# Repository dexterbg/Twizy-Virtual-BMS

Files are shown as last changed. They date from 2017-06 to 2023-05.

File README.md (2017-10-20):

# Twizy Virtual BMS

This is an Arduino library providing an emulation of the CAN communication protocol of the BMS (battery management system) on a Renault Twizy.

By reproducing the system interface of the original BMS, the Virtual BMS enables replacing the original by a custom battery without changing anything else on the Twizy.

Twizy Virtual BMS

The library provides an API to control power limits and charge current, so a wide range of batteries can be used. Even lead-acid is an option.

In the most simple case this can be used without any customization. The provided "SimpleBMS" example shows how to create a very basic battery monitoring by using the Arduino analog ports to measure the battery pack voltage and temperature.

If you'd like to contribute a specific BMS adaptation, please fork and add your code in the examples folder.

## Installation

To download, click the DOWNLOADS button in the top right corner, download the ZIP file. Start the Arduino IDE, select menu Sketch → Include Library → Add .ZIP library, select the ZIP file and click OK. Try out the examples included.

You will also need these libraries:
  - [MCP_CAN_lib by Cory Fowler](https://github.com/coryjfowler/MCP_CAN_lib)
  - …and one of…
    - [TimerOne by Paul Stoffregen](https://github.com/PaulStoffregen/TimerOne)
    - [FlexiTimer2 by Paul Stoffregen](https://github.com/PaulStoffregen/FlexiTimer2)
    - [TimerThree by Paul Stoffregen](https://github.com/PaulStoffregen/TimerThree)

To get the smallest possible ROM & RAM footprint, set `TWIZY_DEBUG_LEVEL` to 0 and `DEBUG_MODE` of the MCP_CAN library to 0. This reduces the core memory usage of the VirtualBMS library to (currently) 8338 bytes ROM and 403 bytes RAM.

## Documentation

  - [API reference](API.md)
  - [History](HISTORY.md)

  - [Twizy CAN object dictionary](https://docs.google.com/spreadsheets/d/1gOrG9rnGR9YuMGakAbl4s97a6irHF6UNFV1TS5Ll7MY)
  - [Twizy BMS protocol](extras/Protocol.ods)

  - [Battery connection scheme](extras/Twizy-BMS-wiring-scheme.pdf)
  - [List of parts](extras/Twizy-Battery-Part-List.md)

  - [SEVCON configuration](extras/SEVCON-Configuration.md)
  - [Charger configuration](extras/CHARGER-Configuration.md)

  - [Prototype (Lead acid)](extras/Prototype-Blazej.md)
  - [Build #2 (Leaf cells)](extras/Blazej2-Leaf-Cells.md)

## Hardware requirements

  - **Battery**: you will need battery cells capable of producing enough voltage and current for the Twizy. You don't need to exactly match the original voltage and power range. The SEVCON G48 series can operate with input voltages from 19.3 to 69.6 V. The Twizy SEVCON is by default configured for a range of 39 to 65 V, but that can be modified (see [SEVCON configuration](extras/SEVCON-Configuration.md)). In standard configuration, the Twizy will draw up to ~330 A or 16 kW from the battery, and recuperate at up to ~70 A or 3.5 kW. If your battery cannot cope with this, you can either use the Virtual BMS to lower the limits or modify the SEVCON configuration.
  
    Pascal is using Nissan Leaf cells, which offer a very good combination of capacity, availability and price. Błażej is using cheap 120 Ah lead acid batteries (price ~400 Euro for a complete set). Klaus will use chinese prismatic cells adding up to ~12 kWh.
    
    **Note**: Klaus offers to organize a bulk order of high capacity prismatic 3.2V LiFePO4 cells in the range of 330€ down to 260€/kWh. For a high performance large capacity setup with 48V 240 Ah (double of the standard battery capacity) a total price only for the battery pack between 2800 and 3200€ seems possible. Each buyer would have the risk in case of failures and should add some spare cells. For details please contact Klaus at <klauszinser@posteo.eu>.
  
  - **BMS**: using a BMS is optional for lead acid batteries but _strongly recommended_ for lithium based batteries. You may pick any BMS, but you should focus on those that can be connected to the Arduino to query the battery state. Our recommendation is picking a good BMS capable of early balancing, monitoring the coulomb (Ah) consumption and calculating the real SOC.

    **Note**: Pascal is developing a **fully integrated BMS solution** supporting various cell & chemistry configurations and containing the complete Twizy interface. The BMS should be available by the end of 2017. Pricing is expected to be around 350 Euro. Using this BMS will both simplify custom battery integration and reduce points of failure. You won't need an Arduino when using this BMS. For details please contact him at <pascal@ripp.li>.

  - **Arduino**: to run the Twizy Virtual BMS you will need some Arduino and some MCP CAN interface. A wide range of hardware options is available. The code perfectly fits into an Arduino Nano leaving enough memory to implement quite complex custom logics. You should pick an MCP 2515 SPI CAN module with at least 16 MHz clock rate. IRQ connection is optional.

    **Note**: Michael offers to customize the Virtual BMS for individual applications and BMS integration. For details please contact him at <dexter@dexters-web.de>.

  - **Connection**: see the [part list](extras/Twizy-Battery-Part-List.md) for relais and connectors needed.

  - **Battery case**: you can use the original Twizy battery case, available as a replacement part from Renault (see part list).
  
    **Note**: Lutz Schäfer offers to build individual custom battery cases offering more space. For details please contact him at <aquillo@t-online.de>.

## Compliance

As the Virtual BMS (as well as the OVMS and other Twizy tools) is based on re-engineering of the CAN protocol, a 100% compliance cannot be reached. There are still unknown fields and codes, look for question marks in the CAN object dictionary for details. Unknown parts may have an effect under special conditions that could not be produced during analysis.

Having said that, the BMS protocol emulation has successfully been tested and is actually being used in real Twizys, enabling the full standard operation using custom batteries.

If you encounter any kind of issue, please send us all details including a full CAN trace for analysis.

## Projects using this library

  - [KlausBMS Twizy Lithium BMS](https://github.com/dexterbg/KlausBMS)

## Authors

This library has been created and is maintained by Michael Balzer (<dexter@dexters-web.de> / https://dexters-web.de/).

The CAN & hardware protocol decoding and reengineering has been done by a joint effort of (in reverse alphabetical order):

  - Lutz Schäfer <aquillo@t-online.de> -- Hardware development
  - Pascal Ripp <pascal@ripp.li> -- Hardware protocol decoding & implementation
  - Bernd Eickhoff <b.eickhoff@gmx.de> -- CAN logging & testing
  - Michael Balzer <dexter@dexters-web.de> -- CAN protocol decoding & implementation

Special thanks to Klaus Zinser <klauszinser@posteo.eu> for support and to Błażej Błaszczyk <blazej.blaszczyk@pascal-engineering.com> for prototype implementation and testing!

Btw: we're all available for **consulting**, **integration** and **customization** jobs.

## Donations



**Donations** to support our efforts and further development are very welcome.  
Please send donations via **Paypal** to: `virtualbms@dexters-web.de`  
**Thanks! :-)**

Donors will be honored in our [Hall of Eternal Fame](DONORS.md), please add a comment to your donation if you'd rather stay anonymous.

## License

This library is free software; you can redistribute it and/or modify it under the terms of the [GNU Lesser General Public License](https://www.gnu.org/licenses/lgpl.html) as published by the Free Software Foundation; either version 3 of the License, or (at your option) any later version.

This library is distributed in the hope that it will be useful, but WITHOUT ANY WARRANTY; without even the implied warranty of MERCHANTABILITY or FITNESS FOR A PARTICULAR PURPOSE.  See the GNU Lesser General Public License for more details.

You should have received a copy of the GNU Lesser General Public License along with this library; if not, write to the Free Software Foundation, Inc., 51 Franklin St, Fifth Floor, Boston, MA  02110- 1301  USA

**Have fun!**

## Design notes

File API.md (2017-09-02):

# API & Usage

Hint: begin with the "Template" example to get a standard usage template including all callbacks.

## Library inclusion

  1. Create a TwizyVirtualBMS object (`twizy` is a good name for this)
  2. Call `twizy.begin()` in your setup function
  3. Call `twizy.looper()` in your main loop:
        ```c++
        #include "TwizyVirtualBMS_config.h"
        #include "TwizyVirtualBMS.h"
        
        TwizyVirtualBMS twizy;
        
        void setup() {
          Serial.begin(115200);
          twizy.begin();
        }
        
        void loop() {
          twizy.looper();
        }
        ```

## Twizy control functions

Note: all control functions validate their parameters. If you pass any value out of bounds, nothing will be changed, an error message will be generated on the serial port and the function will return `false`.

  - `bool setChargeCurrent(int amps)` -- Set battery charge current level
    - amps: 0 .. 35 A current level at battery
    - will stop charge if set to 0 while charging
    - Note: this has a 5 A resolution rounded downwards
    - Note: 35 A will not be reached with current charger generation (max ~32 A)

      | Current level | Power drawn from socket |
      | ------------- | ----------------------- |
      | 35 A          | ~ 2.2 kW                |
      | 30 A          | ~ 2.1 kW                |
      | 25 A          | ~ 1.7 kW                |
      | 20 A          | ~ 1.4 kW                |
      | 15 A          | ~ 1.0 kW                |
      | 10 A          | ~ 0.7 kW                |
      |  5 A          | ~ 0.4 kW                |

  - `bool setCurrent(float amps)` -- Set momentary battery pack current level
    - amps: -500 .. +500 (A, positive = charge, negative = discharge)
  
  - `bool setCurrentQA(long quarterAmps)` -- Set momentary battery pack current level
    - quarterAmps: -2000 .. +2000 (1/4 A, positive = charge, negative = discharge)
    - This is the native BMS current resolution, so no float/division necessary
  
  - `bool setSOC(float soc)` -- Set state of charge
    - soc: 0.00 .. 100.00 (%)
    - Note: the charger will not start charging at SOC=100%
  
  - `bool setPowerLimits(unsigned int drive, unsigned int recup)` -- Set SEVCON power limits
    - drive: 0 .. 30000 (W)
    - recup: 0 .. 30000 (W)
    - Note: both limits have a resolution of 500 W and will be rounded downwards
    - Note: these limits do not apply if the [SEVCON has been configured](extras/SEVCON-Configuration.md) to ignore them
  
  - `bool setSOH(int soh)` -- Set state of health
    - soh: 0 .. 100 (%)
  
  - `bool setCellVoltage(int cell, float volt)` -- Set battery cell voltage
    - cell: 1 .. 16 (the original Twizy battery has 14 cells)
    - volt: 1.0 .. 5.0
    - Note: this does no implicit update on the overall pack voltage
    - Note: cell voltages #15 & #16 will be stored in frame 0x700 (custom protocol extension)
  
  - `bool setVoltage(float volt, bool deriveCells)` -- Set battery pack voltage
    - volt: 19.3 .. 69.6 (SEVCON G48 series voltage range)
    - deriveCells: true = set cell voltages #1-#14 to volt/14
  
  - `bool setModuleTemperature(int module, int temp)` -- Set battery module temperature
    - module: 1 .. 8 (the original Twizy battery is organized in 7 modules)
    - temp: -40 .. 100 (°C)
    - Note: this does no implicit update on the overall pack temperature
    - Note: module temperature #8 will be stored in frame 0x554 byte 7, which is unused on the original pack layout
  
  - `bool setTemperature(int tempMin, int tempMax, bool deriveModules)` -- Set battery pack temperature
    - tempMin: -40 .. 100 (°C)
    - tempMax: -40 .. 100 (°C)
    - deriveModules: true = set module temperatures #1-#7 to avg(min,max)
  
  - `bool setError(unsigned long error)` -- Set display error/warning indicators
    - error: 0x000000 .. 0xFFFFFF (0 = no error) or use a bitwise ORed combination of…

      | Code              | Description                           |
      | ----------------- | ------------------------------------- |
      | `TWIZY_OK`        | Clear all indicators                  |
      | `TWIZY_SERV`      | Set SERV indicator                    |
      | `TWIZY_SERV_12V`  | Set SERV + 12V battery indicator      |
      | `TWIZY_SERV_BATT` | Set SERV + 12V main battery indicator |
      | `TWIZY_SERV_TEMP` | Set SERV + temperature indicator      |
      | `TWIZY_SERV_STOP` | Set SERV + STOP indicator + beep      |

## Info access

  - `int getChargerTemperature()` -- Get internal charger temperature
    - result: -40 .. 100 (°C, resolution 1 °C)
    - Hint: use this to protect the charger against over temperature by reducing the charge current

  - `float getDCConverterCurrent()` -- Get DC/DC converter current level
    - result: 0 .. 51 (A, resolution 1/5 A)

  - `bool isPluggedIn()` -- Get power grid connection status
    - result: true = 230V detected

  - `bool isSwitchedOn()` -- Get key switch status
    - result: true = key turned

## User callback registration

To hook into the control flow you may register custom functions to be called by the VirtualBMS.

All callbacks are optional. See "Template" example for code templates and example attachment.

  - `void attachEnterState(TwizyEnterStateCallback fn)`
    - fn: `void fn(TwizyState currentState, TwizyState newState)`
    - called on all state transitions after framework handling
    - use this to apply custom settings on state changes

  - `void attachCheckState(TwizyCheckStateCallback fn)`
    - fn: `bool fn(TwizyState currentState, TwizyState newState)`
    - called before transitions from `Init`, `Start…` and `Stop…` into `Ready`, `Driving`, `Charging` and `Trickle`
    - if the callback returns false, the transition will be retried on the next 10 ms ticker run
    - use this to check if the battery/BMS is ready for the state transition

  - `void attachTicker(TwizyTickerCallback fn)`
    - fn: `void fn(unsigned int clockCnt)`
    - called by the 10 ms ticker *after* framework handling, i.e. after sending the Twizy CAN frames
    - clockCnt: cyclic 10 ms interval counter range 0 … 2999 (reset to 0 on `Off`/`Init`)
    - use this to add custom CAN sends or do periodic checks

  - `void attachProcessCanMsg(TwizyProcessCanMsgCallback fn)`
    - fn: `void fn(unsigned long rxId, byte rxLen, byte *rxBuf)`
    - called on all received (filtered) CAN messages
    - see `setCanFilter()` for setup of additional custom CAN ID filters

## State machine

The VirtualBMS will do state transitions automatically based on CAN input received from the Twizy.

__TwizyStates:__
  - `Off`
  - `Init`
  - `Error`
  - `Ready`
  - `StartDrive`
  - `Driving`
  - `StopDrive`
  - `StartCharge`
  - `Charging`
  - `StopCharge`
  - `StartTrickle`
  - `Trickle`
  - `StopTrickle`

Normal startup procedure involves the wakeup phase `Init` followed by `Ready`. Depending on the mode of operation requested, this will be followed by one of the `Start…` states with operation mode established resulting in the according `…ing` state.

The shutdown procedure begins with a transition from the `…ing` state to the according `Stop…` state, followed by `Ready` and finally `Off`.

Use the `Error` state to signal **severe problems** to the Twizy and cause an emergency shutdown. `Error` turns off CAN sends and drops the 3MW (ECU_OK) signal. SEVCON and charger will switch off all battery power immediately. To resolve the `Error` state from driving, the user needs to do a power cycle. When used during a charge, the charger will send the BMS into `Off` state, so the charge can simply be restarted by replugging the charger.

**Note**: to indicate **non-critical** problems, do not enter the `Error` state but instead only use `setError()`.

See [protocol documentation](extras/Protocol.ods) for details.

__API:__
  - `TwizyState state()` -- Query current state
  - `FLASHSTRING *stateName([state])` -- Query name of current state / specific state
  - `bool inState(TwizyState state1 [, … state5])` -- Test for 1-5 states
  - `void enterState(TwizyState newState)` -- Force a state change
    - Call `enterState(StopCharge)` to stop a running charge process. Note that `setChargeCurrent(0)` will do so as well.
    - Call `enterState(Error)` to cause an emergency shutdown. Before doing this you should use `setError()` and (if possible) give the user some time to react when in state `Driving`.

__Callbacks:__
  - Before entering states `Ready`, `Driving`, `Charging` and `Trickle` from any other state, the user callback `CheckState()` will be called.
    Exception is entering `Ready` from `Error`, this needs to be done manually anyway (don't expect SEVCON or charger to follow though).
  - After any state transition, the user callback `EnterState` will be called.

## CAN interface access

To hook into the CAN receiver, use `attachProcessCanMsg()` (see above).

Standard filters will pass IDs `0x423`, `0x597` and `0x599`. Three free CAN filters can be used. The mask is fixed to match the whole ID, so you can filter at most three additional IDs at a time.

  - `void setCanFilter(byte filterNum, unsigned int canId)` -- Set a free ID filter
    - filterNum: 1 … 3
    - canId: 11 bit CAN ID i.e. `0x196`

  - `bool sendMsg(INT32U id, INT8U len, INT8U *buf)` -- Send a CAN message
    - Note: will do three retries if TX buffers are full.
    - Returns true if message has been sent, false on error.
    - Retry and error counts are logged every 10 seconds if debug logging is enabled.

## Debug utils

  - `void dumpId(FLASHSTRING *name, int len, byte *buf)` -- Dump a byte buffer in hex numbers
    - name: must be a PROGMEM string, i.e. `dumpId(F("id123"), ...)`
  
  - `void debugInfo()` -- Dump VirtualBMS status, include frame buffers if debug level >= 2
    - this is automatically called every 10 seconds if debug level >= 1

## Extended info frame

Beginning with version 1.3.0, the VirtualBMS supports sending an extended BMS status information on the CAN bus. The frame layout has been designed by Pascal Ripp and Michael Balzer to create a standard base for CAN bus tools like the Twizplay and the OVMS.

The extended info frame is sent at CAN ID 0x700 once per second in all states except `Off`. The frame transports these fields:

  - Byte 0: BMS specific state #1 (main state, i.e. twizy.state())
  - Byte 1: highest 3 bits = BMS type ID (see below), remaining 5 bits = BMS specific error code (see below)
  - Bytes 2-4: cell voltages #15 & #16 (encoded in 12 bits like #1-#14)
  - Bytes 5-6: balancing status (bits 15…0 = cells 16…1, 1 = balancing active)
  - Byte 7: BMS specific state #2 (auxiliary state or data)

The VirtualBMS will not send frame 0x700 unless you set the BMS type. It will also not insert any data into the fields by itself, to fill in data you need to use the API calls as shown below. This way you can use the VirtualBMS library to implement other BMS types as well.

### BMS types

The BMS type is meant for CAN tools to be able to identify the BMS and decode the BMS specific states and error info.

There are currently 7 possible BMS types, defined in `enum TwizyBmsType`:

  - 0 = `bmsType_VirtualBMS` (states and error codes as documented here)
  - 1 = `bmsType_EdriverBMS` (see Pascal's documentation for details)
  - 2…6 = reserved
  - 7 = `bmsType_undefined` (disables frame 0x700)

Types #2…#6 can be assigned to future BMS types.

Please contact us if you want to allocate an ID. Keep in mind: any new BMS type needs support in all CAN tools, so try to reuse one of the already defined BMS types as long as possible.

### BMS error codes (for `bmsType_VirtualBMS`)

Our basic standard proposition covers these error codes (defined in `enum TwizyBmsError`):

  - 0 = `bmsError_None`
  - 1 = `bmsError_EEPROM`
  - 2 = `bmsError_SensorFailure`
  - 3 = `bmsError_VoltageHigh`
  - 4 = `bmsError_VoltageLow`
  - 5 = `bmsError_VoltageDiff`
  - 6 = `bmsError_TemperatureHigh`
  - 7 = `bmsError_TemperatureLow`
  - 8 = `bmsError_TemperatureDiff`
  - 9 = `bmsError_ChargerTemperatureHigh`

Custom error codes can be added beginning at 128. Please contact us if you'd like to add standard error codes.

### API calls

  - `bool setInfoBmsType(byte bmsType)` -- Set informational BMS type
    - bmsType: 0 .. 7 (see above / enum TwizyBmsType)
    - Note: type 7 (bmsType_undefined = default value) deactivates frame 0x700

  - `bool setInfoState1(byte state)` -- Set informational state 1 (main state)
    - state: 0x00 .. 0xFF (specific by BMS type)

  - `bool setInfoState2(byte state)` -- Set informational state 2 (aux state)
    - state: 0x00 .. 0xFF (specific by BMS type)

  - `bool setInfoError(byte errorCode)` -- Set informational error code
    - errorCode: 0x00 .. 0x1F (specific by BMS type)

  - `bool setInfoBalancing(unsigned int flags)` -- Set informational balancing status
    - flags: 16 bits = 16 cells (#16 = MSB, #1 = LSB), 1 = balancing

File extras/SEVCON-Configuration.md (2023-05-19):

# SEVCON Configuration

You do not need to change the SEVCON configuration to use a custom battery if the custom battery delivers voltage and power matching the standard operating range and your SEVCON battery protection has not been disabled.

- The SEVCON G48 series can operate with input voltages from 19.3 to 69.6 V. The Twizy SEVCON is by default configured for a range of 39 to 65 V.
- In standard configuration, the Twizy will draw up to ~330 A or 16 kW from the battery, and recuperate at up to ~70 A or 3.5 kW.

If your battery cannot cope with these limits, you can either use the Virtual BMS to lower the limits or modify the SEVCON configuration.

If you need to set the limits regularly below the standards, consider tuning the Twizy down. Triggering the power limiter will result in a sudden power cutback followed by slowly raising power levels until the limit is reached again. This continues over and over leading to an inconvenient pumping effect.

**Note**: SEVCON write access has been limited by Renault on Twizys (SEVCONs) delivered after June 2016. The write protection applies to all power and driving profile tuning registers, and also to the voltage limits. **If you've got a locked Twizy, your battery should match the standard battery parameters.**

A locked SEVCON will respond to register writes with an error. You can also check the software version (`rs 100a 00`): if it's `0712.0003` or higher, the Twizy is locked.

## Tools

You can configure the SEVCON using…

1. [Official SEVCON tools](http://www.sevcon.com/products/low-voltage-controllers/gen4/)
2. [OVMS](https://github.com/openvehicles/Open-Vehicle-Monitoring-System)
3. [Twizy-Cfg for Arduino](https://github.com/dexterbg/Twizy-Cfg)
4. Generic CANopen editor

The syntax for reading/writing the SEVCON registers slightly varies depending on the software used, but the registers and values are the same.

| Function | Twizy-Cfg | OVMS |
| --- | --- | --- |
| Enter pre-op mode | `p` | `cfg pre` |
| Enter op mode | `o` | `cfg op` |
| Read register | `r <id> <sub>` | `cfg read <id> <sub>` |
| Write register | `w <id> <sub> <val>` | `cfg write <id> <sub> <value>` |

The following command examples use the Twizy-Cfg syntax.

**Note**: negative values currently need to be read and written with value offset 65536 ("complementary"), i.e. -1 = 65535.

## Battery voltage limits

| Register | Description | Default | Scaling | …= |
| --- | --- | --- | --- | --- |
| `2c01 01` | Over voltage start cutback | 992 | 1/16 | 62 V |
| `2c01 02` | Over voltage limit | 1040 | 1/16 | 65 V |
| `2c02 01` | Under voltage start cutback | 656 | 1/16 | 41 V |
| `2c02 02` | Under voltage limit | 624 | 1/16 | 39 V |
| `2c03 00` | Protection delay | 80 | 1/10 | 8 s |

**Example**: to allow voltages down to 35 V, issue…

1. `w 2c02 01 592`
2. `w 2c02 02 560`

**Keep in mind** that the SEVCON derives current levels from allowed power levels (unless configured otherwise, see below). A lower voltage will result in higher currents, take care to lower the power limits as necessary using the `setPowerLimits()` API call when your voltage drops.

## Battery current & power limits

**Note**: these only apply to the driving state, the charger current can be controlled by `setChargeCurrent()` regardless of the SEVCON configuration.

| Register | Description | Default | Scaling | …= |
| --- | --- | --- | --- | --- |
| `2870 01` | Battery current limit source | 4 | see below | BMS |
| `2870 02` | Max discharge current | 500 | 1 | 500 A |
| `2870 03` | Max recharge current | 65336 | -1 | 200 A |
| `2870 04` | Profile 1 level | 0 | 1 | 0% |
| `2870 05` | Profile 2 level | 0 | 1 | 0% |
| `2870 06` | _Max discharge power (derived)_ | i.e. 4608 | 1/256 | 18 kW |
| `2870 06` | _Max recharge power (derived)_ | i.e. 64896 | -1/256 | 2.5 kW |
| `4623 01` | _Calculated recharge current limit (power/voltage)_ | 65493 | -1 | 43 A |
| `4623 02` | _Calculated discharge current limit (power/voltage)_ | 314 | 1 | 314 A |
| `4623 03` | Battery current cutback range | 15 | 1 | 15 A |
| `3813 30` | Battery current recovery speed | 100 | 100/256 | 39.0625 %/s |
| `3813 30` | Battery current cutback speed | 800 | 1 | 312.5 %/s |

**Battery current limit source**:
  - `4`: BMS controls power limits through `setPowerLimits()`, current levels calculated from power levels
  - `3`: Use max currents scaled down by profile level (`setPowerLimits()` disabled)
  - `1`: Use max currents (`setPowerLimits()` disabled)
  - `0`: Limiter off (`setPowerLimits()` disabled)

These registers need pre-operational mode to allow writes.

**Example**: to disable `setPowerLimits()` and set a fixed maximum of 250 A for discharge (driving) and 50 A for recharging (recuperation), issue…

1. `p`
2. `w 2870 01 1`
3. `w 2870 02 250`
4. `w 2870 03 65486`
5. `o`

## SOC based power cutbacks

| Register | Description | Default | Scaling | …= |
| --- | --- | --- | --- | --- |
| `3813 11` | Drive cutback map: SOC 1 | 0 | 1/50 | 0 % SOC |
| `3813 12` | … cutback 1 | 750 | 1/50 | 15 % power |
| `3813 13` | … SOC 2 | 750 | 1/50 | 15 % SOC |
| `3813 14` | … cutback 2 | 5000 | 1/50 | 100 % power |
| `3813 15` | Brake cutback map: SOC 1 | 0 | 1/50 | 0 % SOC |
| `3813 16` | … cutback 1 | 5000 | 1/50 | 100 % power |
| `3813 17` | … SOC 2 | 500 | 1/50 | 10 % SOC |
| `3813 18` | … cutback 2 | 5000 | 1/50 | 100 % power |

The SEVCON applies these linear cutbacks based on SOC additionally to the BMS power limits allowing for a smooth cutback slope. Default is to cutback drive power below 15% SOC, and leave brake power at BMS control.

These registers need pre-operational mode to allow writes.

**Example**: configure full brake power cutback from 90% to 100% SOC:

1. `p`
2. `w 3813 15 4500`
3. `w 3813 17 5000`
4. `w 3813 18 0`
5. `o`

## Other configuration options

Read the SEVCON Gen4 manual for some basic description. The full register set is documented in the SEVCON master dictionary, which is ©SEVCON. It's contained in the SEVCON DVT package.

Most registers of interest for normal tuning have been documented in the [OVMS Twizy SDO list](https://github.com/openvehicles/Open-Vehicle-Monitoring-System/raw/master/docs/Renault-Twizy/Twizy-SDO-List.ods).

**Have fun!**

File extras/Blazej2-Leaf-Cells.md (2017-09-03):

# Build #2 by Błażej Błaszczyk using Nissan Leaf cells

Błażejs second battery is based on used Nissan Leaf cells. Błażej bought a used 2015 Nissan 24 kWh pack for 14000 PLN (~3300 EUR).

The 24 kWh pack consists of 48 modules with ~500 Wh each. He disassembled the pack and managed to put 21 modules into the Twizy (tight fit, original case won't fit around these).

This pack uses a simple standard 14 cell hardware BMS for the cell protection and balancing (hosted on the lower PCB). The upper PCB hosts the VirtualBMS Arduino components, basically following the [example scheme](https://github.com/dexterbg/Twizy-Virtual-BMS/blob/master/extras/Twizy-Battery-Part-List.md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). Cell voltages are measured using voltage dividers over a multiplexer, pack current is measured using a LEM hall sensor and temperatures using LM35. An HC-06 module is included for Bluetooth connectivity.

Real world driving range with this 10.5 kWh pack is around 130-140 km. Due to the higher capacity, the battery voltage is more stable than the original battery, even under high load.

If you'd like to know more, contact Błażej Błaszczyk <blazej.blaszczyk@pascal-engineering.com>.

## Images

(click to zoom)

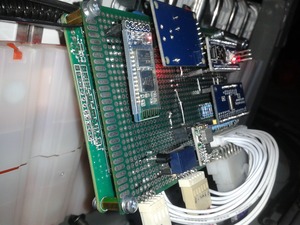
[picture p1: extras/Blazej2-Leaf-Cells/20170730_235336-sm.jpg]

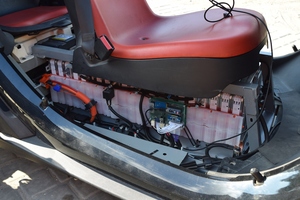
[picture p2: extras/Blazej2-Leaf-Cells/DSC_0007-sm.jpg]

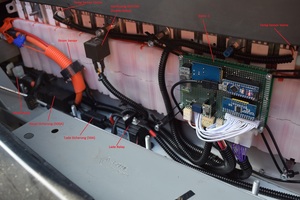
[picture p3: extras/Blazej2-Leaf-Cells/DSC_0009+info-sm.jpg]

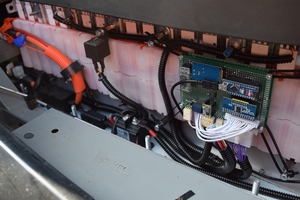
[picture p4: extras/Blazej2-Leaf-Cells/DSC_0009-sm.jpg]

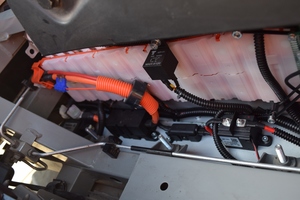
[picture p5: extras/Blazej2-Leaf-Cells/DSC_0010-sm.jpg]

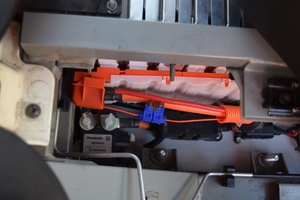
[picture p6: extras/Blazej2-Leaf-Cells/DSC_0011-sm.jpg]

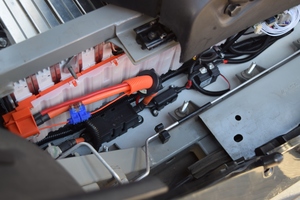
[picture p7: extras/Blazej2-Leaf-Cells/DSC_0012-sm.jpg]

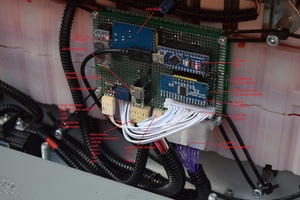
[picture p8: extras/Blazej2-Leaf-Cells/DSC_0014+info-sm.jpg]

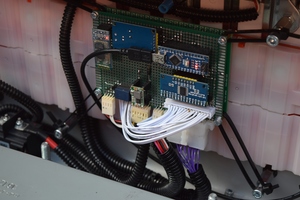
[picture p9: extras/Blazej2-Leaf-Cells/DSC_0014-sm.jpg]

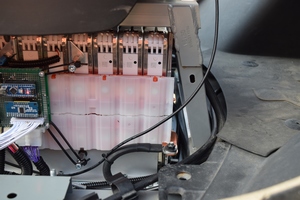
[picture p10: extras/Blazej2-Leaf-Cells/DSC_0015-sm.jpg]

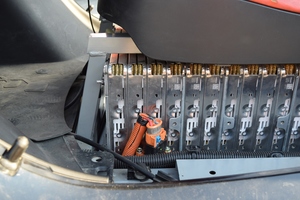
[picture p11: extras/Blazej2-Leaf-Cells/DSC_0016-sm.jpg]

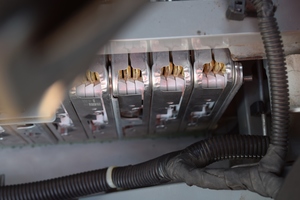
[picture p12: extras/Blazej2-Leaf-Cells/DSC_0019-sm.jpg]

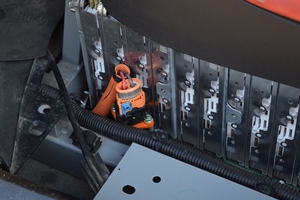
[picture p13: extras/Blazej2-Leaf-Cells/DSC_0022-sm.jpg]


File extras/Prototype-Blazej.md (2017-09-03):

# Prototype build by Błażej Błaszczyk

This is a prototype actually powering Błażejs own Twizy.

It uses four standard 120 Ah lead acid batteries. Range with new batteries is ~ 50-60 km on flat terrain.

No Renault parts have been used. The main power relais is from a fork lift.

There is no BMS other than the Arduino (Nano) itself. The pack voltage is measured using a voltage divider, the pack temperature is measured using an LM35D sensor. SOC is derived from the (smoothed) pack voltage. The software is basically the "SimpleBMS" example from the library with calibration for Błażejs components.

If you'd like to know more, contact Błażej Błaszczyk <blazej.blaszczyk@pascal-engineering.com>.

Please also take a look at [Błażejs build #2](Blazej2-Leaf-Cells.md).

## Videos

(click to watch on Youtube)

Start and GO (https://youtu.be/PRJoss-2DbI "Start and GO")
Drive (https://youtu.be/OG0C9ohnqXw "Drive")

## Images

(click to zoom)

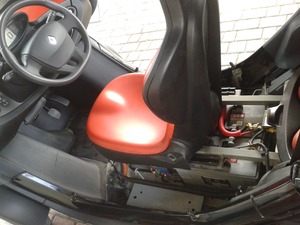
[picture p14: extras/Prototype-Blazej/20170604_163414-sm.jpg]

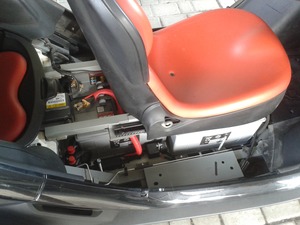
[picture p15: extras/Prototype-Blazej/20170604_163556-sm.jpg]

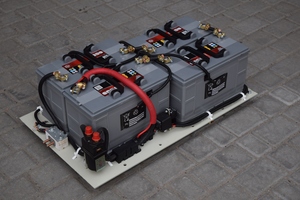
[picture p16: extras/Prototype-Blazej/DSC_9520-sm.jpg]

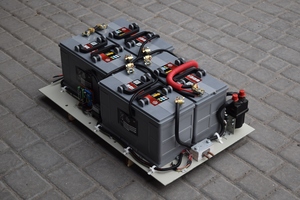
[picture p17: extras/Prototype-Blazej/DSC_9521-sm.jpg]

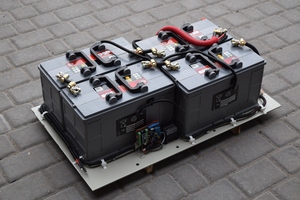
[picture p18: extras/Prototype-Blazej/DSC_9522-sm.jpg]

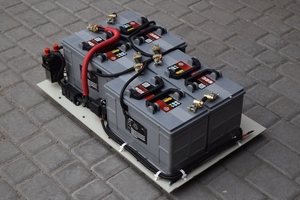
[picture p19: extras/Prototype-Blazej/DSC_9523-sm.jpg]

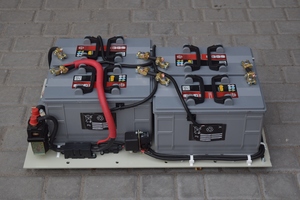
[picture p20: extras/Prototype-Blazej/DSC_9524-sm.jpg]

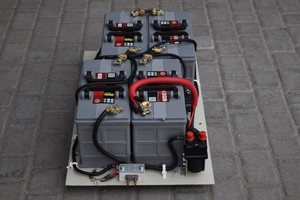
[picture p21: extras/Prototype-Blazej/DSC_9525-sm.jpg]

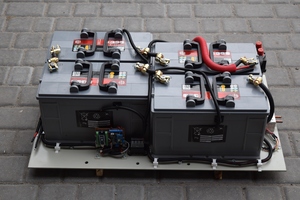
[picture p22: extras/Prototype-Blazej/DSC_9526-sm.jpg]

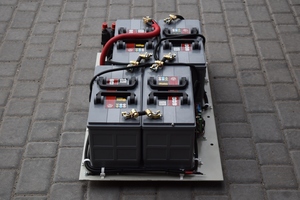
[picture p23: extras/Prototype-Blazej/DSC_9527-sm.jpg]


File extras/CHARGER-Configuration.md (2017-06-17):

# Charger Configuration

You do not need to change the charger if your battery can be charged at the standard voltage and current levels provided by the builtin [IES-Synergy Elips 2000W](http://www.ies-synergy.com/en/chargers/onboard-sealed-chargers/elips-2000w) charger.

- The Elips 2000W can charge with a final voltage of up to 60 V.
- Charge current can be set from 0 - 35 A in 5 A steps.

It may be possible to configure the Elips in the future, at the moment you need to control the charge current and stop the charge process using the `setChargeCurrent()` [API call](../API.md), if your battery cannot cope with the Elips standard charge process.

## Using a custom charger

If you need or want to use a custom charger, take care not to remove the Elips 2000W from the Twizy without further consideration.

The Elips is operating with a specialized firmware and has a crucial role in the Twizy's control protocol.

You can charge a custom battery directly without using the Elips, but for driving and 12V trickle charging the Elips needs to be connected to the battery and CAN bus.

If you're interested in replacing the Elips: creating a "Twizy Virtual Charger" should be possible as well, but has to be done yet.

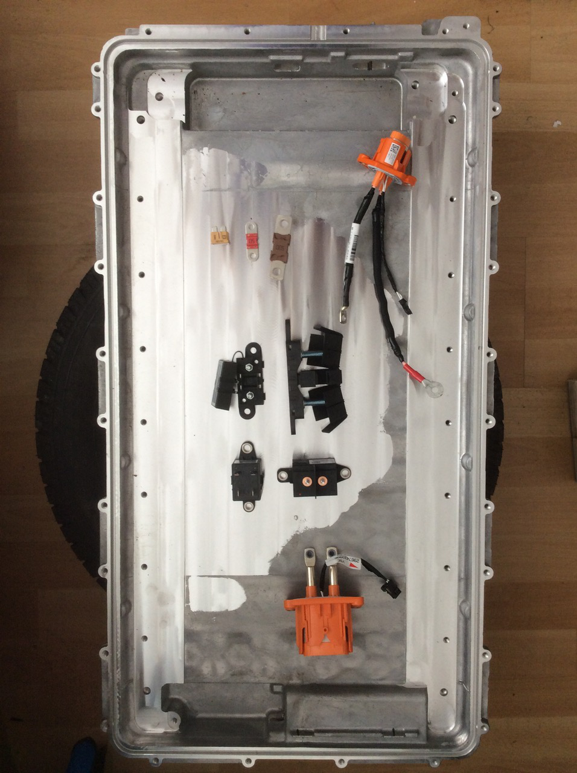
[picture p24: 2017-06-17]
extras/parts/Overview-nm.jpg

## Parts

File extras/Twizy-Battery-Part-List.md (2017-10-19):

# Twizy Battery Part List

For explosion drawings and OE part numbers, see…

1. [partsouq.com](https://partsouq.com/en/catalog/genuine/vehicle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)
2. [catcar.info](https://www.catcar.info/renault/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)

A good source for all parts is [JC Parts](https://www.jcparts.eu/).

## Fuses, connectors and relais

| # | Image | Part | OE number | ~Price |
| --- | --- | --- | --- | --- |
| 1x | 296539341R | Fusible Principal Fltg Ent Chr <br/> *Main fuse 500A* | 296539341R | 4.41 € |
| 1x | 296539051R | Fusible Chargeur Fltg Ent Chrj <br/> *Charge fuse 50A* | 296539051R | 1.67 € |
| 1x | 296535672R | Fusible Apres Contact Fltg Ent <br/> *Precharge fuse 5A* | 296535672R | 1.30 € |
| 1x | 296713282R | Platine Fusible <br/> *Main fuse holder* | 296713282R | 10.48 € |
| 1x | 296712452R | Platine Fusible <br/> *Charge fuse holder* | 296712452R | 7.96 € |
| 1x | 296743399R | Embase Connecteur Batterie Tra <br/> *Main connector (DELPHI)* | 296743399R | 52.22 € |
| 1x | 296746418R | Embase Connecteur Ba <br/> *Charge connector (DELPHI)* | 296746418R | 30.67 € |
| 1x | 296740718R | Embase Connecteur <br/> *Signal connector (Yazaki)* | 296740718R | 86.30 € |
| 1x | 294B16331R | Relais Principal Boitier Cnx P <br/> *Main relais 150A* | 294B16331R | 56.63 € |
| 1x | 294B20431R | Relais Precharge Boitier Cnx P <br/> *Precharge relais 10A* | 294B20431R | 21.19 € |
| 1x | 296156226R | Relais Chargeur Fltg Ent Chrjr <br/> *Charge relais 40A* | 296156226R | 39.96 € |
| | | **Total**  *(prices may change)* | | **~ 310 €** |

Parts may of course be replaced by functionally compatible ones, for example use a fork lift relais for the main power relais (relais & fuses are no special parts). Błażej Błaszczyk has built his [prototype](Prototype-Blazej.md) without using Renault parts. For details please contact him at <blazej.blaszczyk@pascal-engineering.com>.

  - The `296740718R` signal connector is Yazaki part no. [7282-8854-30](http://connectors-catalog.sys.yzk.co.jp/yazaki-web/servlet/SubServlet_e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) (contact terminals sold separate).
  - The `296743399R` main power connector is DELPHI part no. [F473110](http://ecat.delphi.com/feature?search=F473110), with contact terminals [F176600](http://ecat.delphi.com/feature?search=F176600).
  - The `296746418R` charger power connector is DELPHI part no. [F873110](ecat.delphi.com/feature?search=F873110), with contact terminals [15516298](http://ecat.delphi.com/feature?search=15516298).

## Casing

| # | Image | Part | OE number | ~Price |
| --- | --- | --- | --- | --- |
| 1x | 295F00162R | CARTER SUP BATTERI	<br/> *Casing cover* | 295F00162R | 129 € |
| 1x | 295F19016R | CARTER INF BATTERI <br/> *Casing base* | 295F19016R | 216 € |
| 1x |  | JOINT ETC CARTER B <br/> *Casing seal* | 295G32560R | 46 € |
| | | **Total**  *(prices may change)* | | **~ 390 €** |

**Note**: Lutz Schäfer offers to build individual custom battery cases offering more space. For details please contact him at <aquillo@t-online.de>.

__Sizes__:
  - Standard Renault Box: 724 x 368 x 208 mm
  - Lutz-Box V1 (without car modification): 745 x 400 x 245 mm
  - Lutz-Box V2 (car modification necessary): 745 x 480 x 245 mm

## Arduino

**Note**: if you plan to use **Pascals integrated Twizy BMS**, you won't need an Arduino. The integrated BMS also implements the Twizy protocol.

For a basic setup you'll need an Arduino, a CAN interface and a relais to switch the 3MW signal.

If you want/need to measure cell voltages and temperatures with the Arduino, you will most probably need some analog input extension. A very simple and cheap setup for up to 16 cells is to use an analog multiplexer based on the CD74HC4067 chip.

Standard Arduinos can be powered from 12V, but will burn the voltage difference (convert to heat), so a step-down voltage regulator is highly recommended. The [Pololu A-Star SV series](https://www.pololu.com/category/149/a-star-programmable-controllers) has on-board step-down regulators suitable for a 12V supply.

Using an Arduino Uno style main board with shields reduces soldering requirements but needs more money and space than for example a Nano based board with break out components.

Keep in mind for all setups, this is an automotive application: expect high levels of mechanical stress due to road shocks and temperature expansion/contraction. Protect your electronics against humidity.

**Price note**: there are lots of cheap Arduino clones available. These can of course be used as well. Expect a lower build quality, so better order some spares (always a good idea).

### Example basic Uno/Shield setup

| Category | Component | ~Price |
| --- | --- | --- |
| Main+Power | Pololu A-Star 32U4 Prime SV | 24.95 € |
| CAN | Seeed Studio CAN-BUS Shield v1.2 | 24.95 € |
| Relais | Seeed Studio Relais Shield V3.0 | 21.95 € |
| **Total** | | **~ 72 €** |

### Example basic Nano setup

| Category | Component | ~Price |
| --- | --- | --- |
| Main | Arduino Nano V3 clone | 4.95 € |
| I/O | Arduino NANO Screw Terminal Expansion Board | 4.95 € |
| CAN | NiRen MCP2515_CAN (TJA1050) | 4.50 € |
| CAN | … 16 MHz quartz | 0.23 € |
| Relais | 5V 2 Channel Relay Shield | 2.95 € |
| **Total** | | **~ 18 €** |

### Example components

| Category | Component | ~Price |
| --- | --- | --- |
| Main | Arduino Uno R3 | 20.80 € |
| Main | Arduino Nano V3 | 23.80 € |
| Main+Power | Pololu A-Star 32U4 Prime SV | 24.95 € |
| Power | Pololu 5V, 2.5A Step-Down Voltage Regulator D24V22F5 | 8.95 € |
| CAN | Seeed Studio CAN-BUS Shield v1.2 | 24.95 € |
| CAN | NiRen MCP2515_CAN (TJA1050) <br/> *Note: these come with 8 MHz quartz, you should replace this with a 16 MHz type* | 4.50 € |
| Relais | Seeed Studio Relais Shield V3.0 | 21.95 € |
| Relais | 5V 2 Channel Relay Shield | 2.95 € |
| I/O | Adafruit Proto-Screwshield | 15.50 € |
| I/O | Arduino NANO Screw Terminal Expansion Board | 4.95 € |
| I/O | SparkFun Analog/Digital MUX Breakout - CD74HC4067 (16 Channel) | 4.95 € |
| I/O | Adafruit ADS1015 12-Bit ADC - 4 Channel | 10.95 € |
| I/O | Mayhew Labs Extended ADC Shield | 30 € |
| I/O | Seeed Studio RS232 Shield | 12.50 € |
| I/O | HC-05 Bluetooth module | 6.00 € |

### Example Arduino wiring scheme

This example setup could be used for a battery pack with a very basic BMS that does only cell protection and has no communication interface. So the Arduino is used to monitor cell voltages, pack current and temperature. This is all optional -- basically you could derive the SOC estimation from just the overall pack voltage as well.

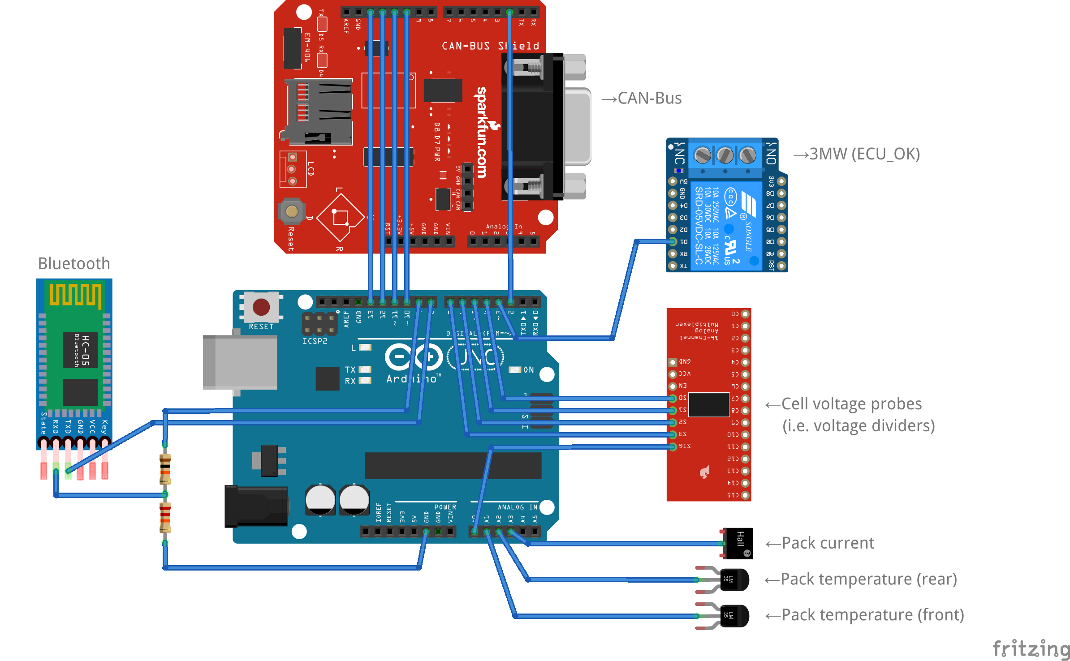
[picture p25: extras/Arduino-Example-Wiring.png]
Arduino Example Wiring


  - [PDF](Arduino-Example-Wiring.pdf)
  - [Fritzing file](Arduino-Example-Wiring.fzz)

The Fritzing diagram only shows the I/O connections, but there's little more: add power supply and enable the multiplexer permanently (connect pin EN to VCC). Obviously, when using a CAN shield like shown in the diagram, it's wiring is done by mounting the shield.

The bluetooth module is optional but neat, it enables to check your VirtualBMS output with a smartphone.

Cell voltages can be measured using the multiplexer shown and simple voltage dividers measuring the stacked voltages, but keep in mind you lose precision by the scaling. The Arduino analog ports provide 10 bit resolution on the voltage range of 0-5 V = ~5 mV. So when scaling to 60 V, resolution drops to ~60 mV. This is good enough to detect a bad cell, but not for precise health monitoring. You may use ADC shields with higher resolution and/or differential voltage probes to get the single cell voltages, but when thinking about this, take a look at specialized battery monitoring chips like the MAX11080 or LTC6811 first.

The pack current can be measured using either a shunt (with an [instrumentation amplifier](http://www.vwlowen.co.uk/arduino/current/current.htm) or an [ADC with preamp](http://arduinotronics.blogspot.de/2015/05/reading-current-shunt-with-arduino.html)) or a hall sensor module like the [LEM HAC 600-S](http://www.lem.com/hq/de/component/option,com_catalog/task,displaymodel/id,64.05.52.000.0/) or the [Tamura L06P400S05](http://www.tamuracorp.com/clientuploads/pdfs/engineeringdocs/L06PXXXS05.pdf). The LEM outputs -4…+4 V so needs to be mapped to the Arduino's 0…5 V (i.e. using an offset voltage divider), the Tamura outputs 0…5 V (2.5 V = 0 A) so can be used directly.

The temperatures can be measured using LM35 sensors. Depending on the variant used, voltage may need to be mapped to the Arduino input. If you want to measure every single cell temperature, you can also extend the setup by another MUX for the temperature sensors -- just use the same address pins as for the voltage MUX.

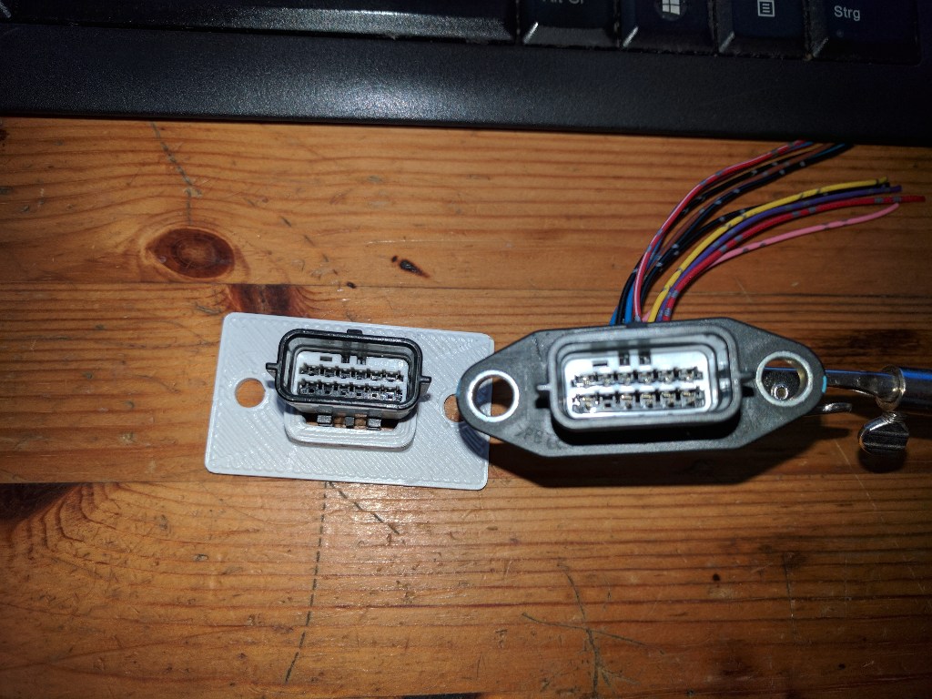
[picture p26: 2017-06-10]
extras/parts/296740718R-tapping.jpg

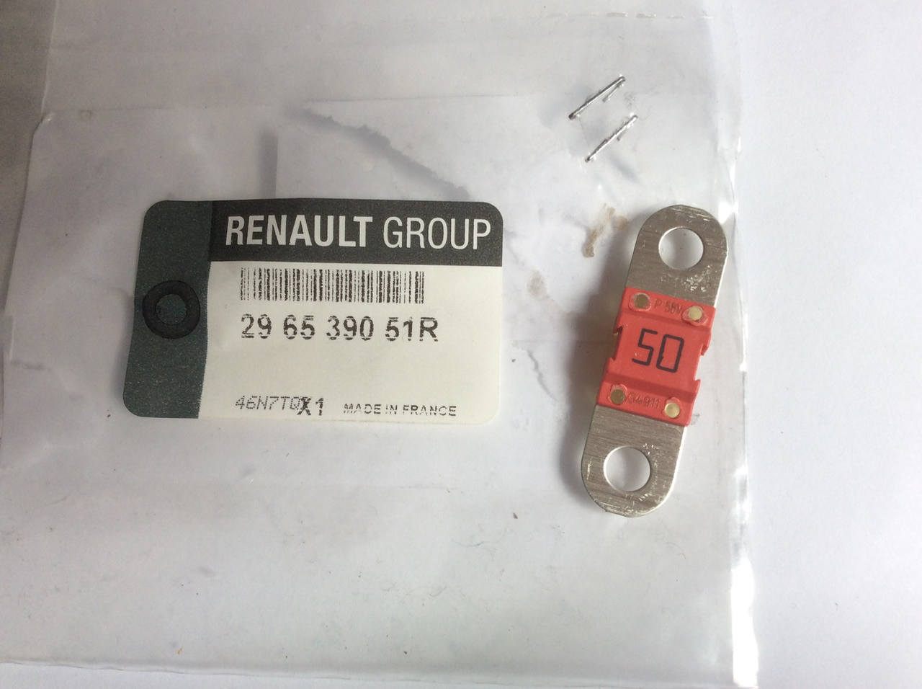
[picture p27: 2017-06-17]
extras/parts/296539051R-nm.jpg

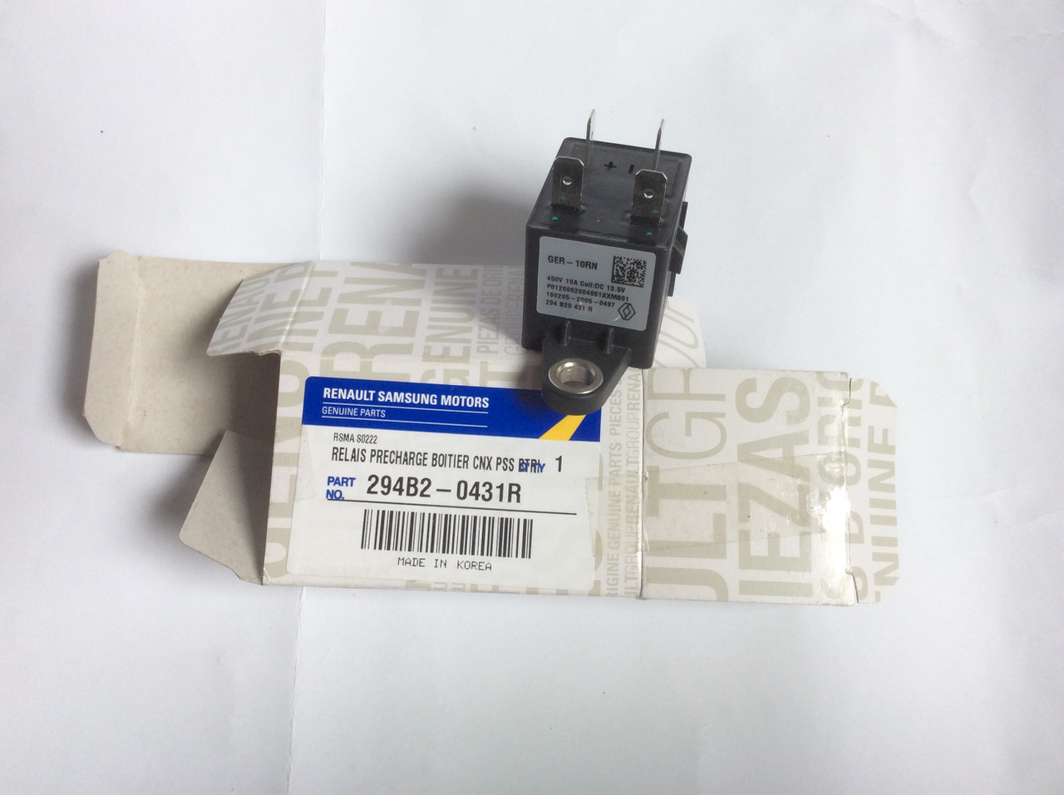
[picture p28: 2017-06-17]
extras/parts/294B20431R-nm.jpg

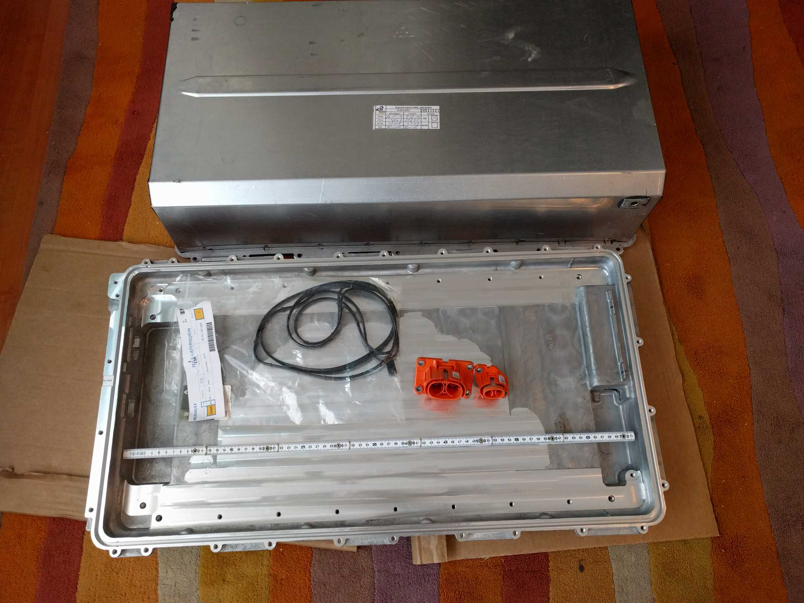
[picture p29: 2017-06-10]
extras/parts/295F00162R-nm.jpg

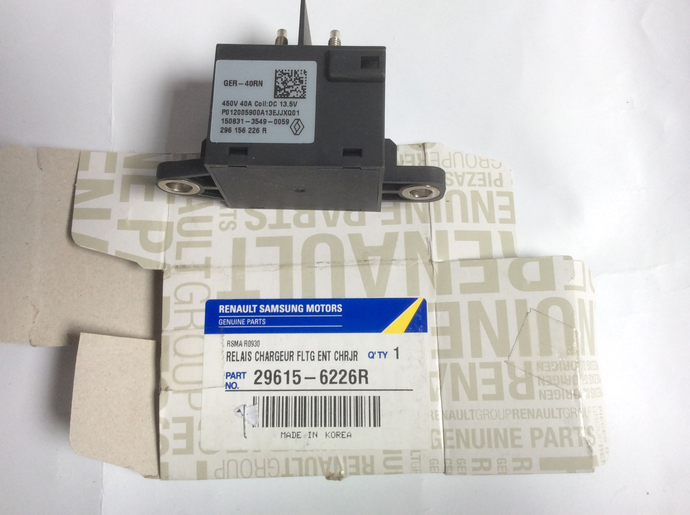
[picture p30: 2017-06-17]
extras/parts/296156226R-nm.jpg

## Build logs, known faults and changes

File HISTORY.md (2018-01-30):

# History

## Version 1.4.4 (2018-01-21)

- Solved issue #1 (charger compatibility)
- Closer reproduction of init phase frames
- Detection of wakeup & shutdown by CAN activity

## Version 1.3.0 (2017-08-30)

- Added support to generate extended info frame 0x700
- New API calls: setInfoBmsType(), setInfoState1(), setInfoState2(), setInfoError(), setInfoBalancing()
- Added support for module temperature #8 and cell voltages #15/#16

## Version 1.2.1 (2017-08-17)

- New API calls stateName(), stateName(state)
- No out of bounds error messages in TWIZY_DEBUG_LEVEL 0

## Version 1.2.0 (2017-07-29)

- Ticker increments clockCnt on exit (first hook call with clockCnt=0)
- Protocol startup phase closer to original:
  - id155[0] set to 0xFF on Init
  - Transition from Init to Ready after 100 ms
  - 3MW timing changed to 200 ms
  - id155[3] update coupled to 3MW switch
- Added API functions to query charger infos:
  - int getChargerTemperature();
  - float getDCConverterCurrent();
  - bool isPluggedIn();
  - bool isSwitchedOn();

## Version: 1.1.0 (2017-06-20)

- Added support for Timer2 & Timer3 (see config header)
- Added `setCurrentQA()` API call (native=fast 1/4 A resolution)

## Version: 1.0.0 (2017-06-17)

- Conversion to Arduino library
- Added CAN RX callback `ProcessCanMsg`
- Added `setError()` and error codes
- Using ROM strings to save RAM
- Configurable debug output level
- Added example Template
- Added example SimpleBMS
- Added `setCanFilter()`
- Added API documentation
- Added hardware documentation
- Added SEVCON configuration info
- Added charger configuration info
- Protocol documentation update on error codes
- Added `Error` state for emergency shutdowns
- Ticker callback also called in state `Off`
- Added donation info & donors file
- Added parts images
- Added inState() test functions
- Added Arduino components to parts list
- Added overview text for Blazejs prototype

## Version: 0.2 (2017-06-06)

- 3MW pulse cycle
- Separate states for trickle charging
- CAN TX retries
- Added bmsTicker() callback

## Version: 0.1 (2017-06-04)

- Initial release

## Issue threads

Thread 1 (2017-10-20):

Charger compatibility

dexterbg, 2017-10-20:
Blazej has reworked a handfull Twizys using the VirtualBMS and has found an issue: the current VirtualBMS implementation does only work with chargers up to generation 5 (charger label: "Ind …"). Generation 8 and newer do not work, generations 6 & 7 have not yet been tested.

The effect is the charger being stuck in the first protocol init step (F0-A2 in 597h) for both driving and charging. We've found no differences yet on the CAN side. We also tried some variations on the 3MW timing, but without success.

Please reply if you can share some insight or information on this problem or can help solving this issue.

Jekyll555, 2017-10-31:
As I did not find chargers around with Ind >5:
Does this change in Charger implementation possibly coincident with the SEVCON (inverter) register locks (>06/2016)?

dexterbg, 2017-11-01:
No. Charger evolution timeline is roughly:
2011 - Ind 04 / PIE 296 054 684R -- works
2012 - Ind 05 / PIE 296 055 169R -- works
2013 - Ind 06 / PIE 296 052 118R -- unknown
2013 - Ind 08 / PIE 296 058 331R -- doesn't work
2014 - Ind 10 / PIE 296 050 463R -- doesn't work

klausz, 2017-11-01:
When talking to a Renault Dealer and looking what Power Supply has to be installed in case of a failure for a June 2012 Twizy (one of the first models) the following:
- the newest Power Supply can be installed. Means there is only one Power Supply Type for all Twizy (the earliest and the latest Models)
- when asking if there are additional parts needed, nothing was on the spare part/exchange list
- also they made no firmware update etc (they are not aware that there is a change).
Min one failed power supply was exchanged not long ago (from an old Twizy) from them.
((When remembering correct, in the Twizy forum one person, who had exchanged the Power Supply himself, reported that the vehicle was not working)).

If everything above is correct (really?),
- the Renault/Sevcon/LGChem firmware is working with all power supplies
- whilst the Arduino Virtual BMS is not.
- We currently dont know about the edriver BMS.

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

dexterbg, 2018-01-30:
The issue has been solved by Bernd with verification by Blazej.
The cause was a missing handshake in id155[1], the high nibble needs to go 9→A→9 along with the 3MW pulse.
→ Commit f45ee40ae2fb9b89ab5795ab270df76c209e506f

Closed 2018-01-30.

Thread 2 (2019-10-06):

Need help. Twizy charger issue

Kamsta99, 2019-10-06:
Hi, my twizy is stuck charging at max 5A, tried a lot off settings and a lot of BMS (Blazej BMS, KlausBMS,  SimpleBMS). Unfortunely im still not so advanced in coding on Arduino, but i changed setChargeCurrent() value to 10 A min in code to make sure but no success. Charging percentage are not updated, i need to switch off->on. Any sugestions ?

dexterbg, 2019-10-06:
That sounds pretty confused. You normally cannot simply switch the software without understanding how they each work and what they need.

SimpleBMS uses a voltage reading to derive SOC, and the SOC to derive the allowed charge current. So if the voltage reading isn't configured correctly or doesn't work, both SOC and charge current will likely also not work. BlazejBMS is tailored to a 4 "cell" lead acid configuration, and KlausBMS to a 16 cell LFP setup.

All example implementations do extensive logging via serial. My suggestions are:
a) describe your setup
b) provide the debug log

Kamsta99, 2019-10-06:
At first i want to thank you for reply, i done battery using Li-Ion batteries LEV40 14cellsx3. Everything except charging works fine (driving no errors).
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
I did case for batteries.
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
Also using oryginal sockets
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
No errors on LCD

Kamsta99, 2019-10-06:
Also i got these debugs when charging
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

dexterbg, 2019-10-06:
Nice images, but without any substantial info on your actual setup.

a) Do you use a real BMS or the Arduino as the BMS?
b) How do you read the battery sensors, which sensors do you have?
c) Your log only shows the VirtualBMS core debug output, where are the debug outputs of the BMS model chosen?
d) And which one is that now? And how is it configured / modified for your hardware?

Kamsta99, 2019-10-06:
a) Im using Arduino Nano as BMS
b) We did voltage divider from 60V ->4,5V like note in code also used vcore show same result like voltage meter
c) I got log only in idle state Vcore, soc and temp looking at code i should have more ...
d) I had most success on SimpleBMS, there files, i changed battery voltage
[SimpleBMS.zip](https://github.com/dexterbg/Twizy-Virtual-BMS/files/3694847/SimpleBMS.zip)

dexterbg, 2019-10-06:
OK, that gets us one step further. Now I need the actual full log output of a charge attempt.
The SimpleBMS log should show the measurements and data derived from the measurements once per second from bmsTicker().

Kamsta99, 2019-10-07:
There is everything i got via log
https://www.youtube.com/watch?v=UT8BhkOUG44&list=LLmkOltXakQK5IzsuK87Dk0A&index=2

dexterbg, 2019-10-07:
OK, there's a bug in the SimpleBMS bmsTicker function.
In SimpleBMS.ino, please change the ticker line 107 from…
```C
  if (twizy.inState(Off) && (clockCnt % 100 == 0)) {
```
…to…
```C
  if (!twizy.inState(Off) && (clockCnt % 100 == 0)) {
```
…then get another log.

dexterbg, 2019-10-07:
As the whole ticker did only run in state "Off", that may have been the cause for your issue with SimpleBMS as well.

But that bug is only present in SimpleBMS, not in BlazejBMS or KlausBMS, so let's see where you get now.

Kamsta99, 2019-10-07:
WOAH 32A charging working and percentage goes up. Grab my generous donate.

Kamsta99, 2019-10-07:
Nah i miss comment section in donate. I dont want to anonymous but Kamsta99 👍

dexterbg, 2019-10-07:
You're welcome. Please send images of the build process and final result if you'd like me to include your build as another showcase.

Kamsta99, 2019-10-07:
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
Trying to understand how arduino works
https://dl3.pushbulletusercontent.com/iGrAU85naZRIOcvgQ866JFKJROkRwXkn/20190831_203701.jpg
also some hardware problems we cant get GO light at first

dexterbg, 2019-10-07:
Please collect everything as a ZIP and send me that by email for the inclusion. Thanks!

abdurauf16, 2020-08-17:
my twizy is off but stop and n are on

abdurauf16, 2020-08-19:
hello, I have a twizy on the ride, the light is off, the go light is on, stop can, or you will send a sketch for acid batteries for a renault twisi

abdurauf16, 2020-08-19:
hello, I have a twizy on the ride, the light is off, the go light is on, stop can, or you will send a sketch for acid batteries for a renault twizy please help me dwxterberg please help

Abdurauf1234, 2022-02-02:
pleas help how to do virtual bms

Abdurauf1234, 2022-02-03:
I bought a Renault Tweezy without BMS and for 4 years I can’t make a virtual BMS, I can make a video on how to make your first virtual BMS based on acid batteries, I would buy a Renault Twizy accumulator, but I need to bring it from Korea if it will cost about 2000 to bring it from Korea to our country $ 3000 and in our country on average they earn $ 200 help please make a virtual BMS from acid batteries, you can throw off the connection diagram of the components

Closed 2019-10-07.

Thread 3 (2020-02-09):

Hi Dexter again i have problem with SimpleBMS ...

Kamsta99, 2020-02-09:
Hi friend, i need help a little bit, Twizy driving fine but my charger sometimes randomly shutdown ... solution is to just unplug and plug again, but this force to babysit your car, is there any possible solution via code ? Someting like loop to start charging again if SOC below value ? Im not scripter or coder sadly.
[SimpleBMS.zip](https://github.com/dexterbg/Twizy-Virtual-BMS/files/4178125/SimpleBMS.zip)

dexterbg, 2020-02-11:
Great to hear it still works.

There is most probably a simple solution to this, but we should first get a clue about the reason for the aborts. Can you provide a debug log (`TWIZY_DEBUG_LEVEL` set to 2) of a charge process including an abort event?

Do you use the original Renault charger? Many Twizy have issues with the first generation of these. Maybe your charger is about to die. Most issues result from the charger getting too hot, in some cases it could be traced down to a blocked/malfunctioning fan. Did you check if the fan works normally?

You also should open and check the connector from the charger to the battery, there have been reports of these corroding / burning / melting.

Kamsta99, 2020-02-11:
Glad to hear you :D
Im using original charger
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
Charger was dismantled and cleaned, fan was also cleaned some time ago.
 I will try to record this log today but its totaly random

dexterbg, 2020-02-11:
Yes, that's version 06 from 2013, IIRC still the first generation (second begins with Ind 08).
Fingers crossed it doesn't die now, you certainly won't get a replacement on warranty…

Kamsta99, 2020-02-11:
I cant reproduce problem now, today charging without shutdown as i say its random. Did you have idea how to fix this by extra bits of code ? Code seems less expensive than charger

Kamsta99, 2020-03-11:
Hi after a longer while, i tried debug mode 2 but using this make my car unable to drive or charge, after dump everything crash (like after 10 seconds after run). My charger from 2013 likely died some days ago, i installed another which i bought from internet, charger from 2016, everything working well but still finish charging before reaching 100%, any ideas ?

dexterbg, 2020-03-15:
Well, if you bought a used charger, you cannot know if that doesn't have the same issue already…
Debug mode 2 normally works, no idea about the crash. Regarding the charge stops, another (maybe better) option would be a separate CAN log.

Kamsta99, 2020-03-15:
Debug mode 2 make my twizy not able to charge or drive, when dump appear via bluetooth GO light disappear and if trying to drive km/h also. Charger (new one) working well, sometimes shutdown near 80%-90%. Separate can log how to do that ?

dexterbg, 2020-03-15:
Use some separate CAN logging device. Needs to be capable of 500 kbit CAN logging. You can use my https://github.com/dexterbg/CanLogger, but take care to turn on compiler speed optimization, comment out the logic inputs, and/or use a faster Arduino board.

Kamsta99, 2020-04-25:
I have no clue how to do that, tried some things, but no success. I started to doing code solution.
`    }
    if (twizy.isPluggedIn() == 1) {
      if (twizy.inState(Off) && (soc <= 98)) {
        Serial.print(F("bmsEnterState: forcing charging "));
        twizy.enterState(StartCharge);
      }
    }`

Kamsta99, 2020-04-25:
Changed code a bit got 3MW working, but still keeps staing in off state
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

dexterbg, 2020-04-26:
Are you trying to (re-)start the charge from the BMS? That will not work. The BMS doesn't start the charge, the charger does. The BMS can tell the charger to reduce current or stop, but not to start.

My idea was there is possibly something causing a stop charge command, but you should see that in the BMS log. If you don't, the charger stops by itself, and then the BMS cannot do anything about that.

There's just one slight possibility that may also cause the charger to abort: if your Arduino has a timing issue, i.e. cannot sustain exact 10 ms intervals for the communication. See config #define TWIZY_CAN_CLOCK_US. Try reducing and increasing this in small steps around the default of 10000.

Kamsta99, 2020-04-26:
Problem happen unfortunnelly on 4 different complete arduino boards

dexterbg, 2020-04-27:
I still think you need to capture a debug log and/or CAN log of an abort event first to get a hint about the source of the issue.

Kamsta99, 2020-06-08:
https://streamable.com/ivw80g
This is how this looks on twizy debugmode 2
Still no can logging sadly

Abdurauf1234, 2022-02-02:
Hello l have Renault twizy but not bms how to do simple l make simple bms but don.t working

Abdurauf1234, 2022-02-03:
how to make a virtual bms for tweezy acid or gel I need a virtual bms for the answer please

Abdurauf1234, 2022-02-03:
don.t close please

Abdurauf1234, 2022-02-03:
you have instagram or facebook please help

Abdurauf1234, 2022-02-03:
I bought a Renault Tweezy without BMS and for 4 years I can’t make a virtual BMS, I can make a video on how to make your first virtual BMS based on acid batteries, I would buy a Renault Twizy accumulator, but I need to bring it from Korea if it will cost about 2000 to bring it from Korea to our country $ 3000 and in our country on average they earn $ 200 help please make a virtual BMS from acid batteries, you can throw off the connection diagram of the components

Abdurauf1234, 2022-02-03:
please help

Abdurauf1234, 2022-02-03:
my email abduraufvaliev@gmail.com

Abdurauf1234, 2022-02-04:
dexterberg

Closed 2022-02-03.

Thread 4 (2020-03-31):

Start signal fault

Rox50055, 2020-03-31:
Hello!
Thanks to your code we got super far with our twizy! most fault codes are gone, but some annoying ones stick.

The first one is like the title: Start signal Fault P0412.
Along that code we also got: Power supply relay Fault P0218. We got a relay connected to the Sevcon relay wires on the plug coming from the Twizy.
The red STOP light is on and and the battery logo with ! on it, no ERROR though.

For now we are just connecting the bare minimum to test if it still works but to no success yet.
I was wondering if you might know a fox for this issue?

Hope to hear from you soon!
Greetings Kenneth

dexterbg, 2020-04-04:
Kenneth,

the fault sounds like you only connected only one of the SEVCON supply relays.

I've attached a draft of the Uno example extended by the Yazaki plug and relays. Check your setup against this.

Regards,
Michael

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

Rox50055, 2020-04-11:
Thanks for the reply!
Making these connections solved the No start signal problem. But sadly the twizy still doesnt work.

We now got the fault P0216/DF181 "Power Relay Charger" and it wont activate the relays to power the sevcon or or other components. When I have my can reader attached with live data I can see the states of all relays and by default it's Open and when I manually power it, it switches to Closed. Meaning that the feedback works.

My thought is that the charger is not giving out the OK signal for it to work or not getting all the proper information. It is a Twizay and charger from 2012, so there shouldn't be any software locks.

I hope that you might know a solution to this!
Thanks in advance

Best regards,
Kenneth

dexterbg, 2020-04-13:
The charger power relay is controlled directly by the charger, it's normally activated during the startup handshake with the BMS (not sure at which step, but I'd guess immediately after the initial communication). Compare the handshake to the protocol document. If the handshake looks normal, there must be some electrical fault. Check all wiring, connections and fuses involved.

Tudy1983, 2020-05-04:
Can have the code please compiled I'm trying to figure out how this is done I'm new in this project I'm still learning like this I can make my own battery  thanks

Rox50055, 2020-05-04:
Hey.
Sadly we have determent that the charger is broken (it's the oldest model) and that's why it doesn't work. The new problem is that we can't find a new, old one that will work with the VBMS you wrote according to what I read on your pages. (The 2016+ models)

We also tried to control  the sevcon direcly with no success since it's also expects a Clear from over the canbus.

I do not have the equipment or know how to decode canbus signals, nor do we have a working twizy. Maybe you know a way to remove the charger completely out the system?

Hope to hear from you soon again!
If this way doesn't work than we probably have to just get rid of it all and get a universal ESC/Motor controller.

Best regards,
Kenneth

Tudy1983, 2020-05-04:
Wath I was mean is the code for arduino I'm tryna o se the difference between them I'm trying to build a virtual bms an I think that somewhere I made a mistake

dexterbg, 2020-05-09:
Kenneth,

> Sadly we have determent that the charger is broken (it's the oldest model) and that's why it doesn't work. The new problem is that we can't find a new, old one that will work with the VBMS you wrote according to what I read on your pages. (The 2016+ models)

That is not correct. All charger models are supported.

> We also tried to control the sevcon direcly with no success

You cannot operate the Twizy without the charger, as the charger runs a special Renault firmware that works as the central power up controller for the whole system. There's a chance to implement a virtual charger as well, based on the information provided here. But don't expect that to be done by me.

Regards,
Michael

xury77, 2021-07-15:
I have same problem. Did you resolved it?
I also have a question about 3MW relay. It should be activated (shorted C with NO) by LOW gpio3 state or HIGH? I bought one witch is activated by gnd signal. Its correct?

dexterbg, 2021-07-16:
@xury77 The code assumes HIGH (1) to activate the relay. You can try exchanging 0/1 on all ``digitalWrite(TWIZY_3MW_CONTROL_PIN, …)`` calls if your relay needs it the other way around. You'll probably also need an init to 1 after ``pinMode(TWIZY_3MW_CONTROL_PIN, OUTPUT);``.

Regarding the fault issue, maybe @Rox50055 can provide some info on his advances.

xury77, 2021-07-16:
Hi Michael. Could you take a look at this diagram. Is the voltage divider is correct? Or I have to swap resistors?
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

dexterbg, 2021-07-17:
Looks correct to me. Be aware the voltage divider is a rather simple monitoring approach, it didn't work very well for Klaus. Readings will be off whenever the BMS activates a cell bypass. There are better solutions based on Opamps or dedicated ICs like the LTC6803. Best option is to use a BMS that can give you the cell voltages via some communication interface.

kosemrt, 2021-10-04:
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

Hello could you share this relay' fritzing file please?

abdurauf12345666, 2022-02-03:
I bought a Renault Tweezy without BMS and for 4 years I can’t make a virtual BMS, I can make a video on how to make your first virtual BMS based on acid batteries, I would buy a Renault Twizy accumulator, but I need to bring it from Korea if it will cost about 2000 to bring it from Korea to our country $ 3000 and in our country on average they earn $ 200 help please make a virtual BMS from acid batteries, you can throw off the connection diagram of the components

abdurauf12345666, 2022-02-03:
please help me

Closed 2022-02-03.

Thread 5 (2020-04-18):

Battery charge level

bakrimo, 2020-04-18:
Hi friend
I did simple bms (lead acid battery)
Problem that the charge level not showing nothing
Any suggestions what I did wrong
Thanks

dexterbg, 2020-04-18:
https://www.youtube.com/watch?v=x40XnMGI75M

bakrimo, 2020-04-19:
Thank you for your replay
The battery level on dashboard it shows 0v charge like no battery

dexterbg, 2020-04-20:
That's what you initially wrote. What about details like hardware setup, software configuration & serial debug log content?

bakrimo, 2020-04-21:
What find out that the problem with hardware
Mcp2515_can bus that I have is 8mhz
Instead of 16mhz
Is there anyway to let it work with 8mhz

dexterbg, 2020-04-21:
Looking into the configuration file may help…

https://github.com/dexterbg/Twizy-Virtual-BMS/blob/master/examples/SimpleBMS/TwizyVirtualBMS_config.h#L33

But earlier attempts with 8 MHz failed, that's why I recommend 16 MHz. You normally can exchange the crystal on an 8 MHz module.

bakrimo, 2020-04-27:
I replaced the 8mhz crystal with 16mhz but still same problem is there anyway to get shem of Arduino nano and mcp2515 connection

dexterbg, 2020-04-27:
I don't understand you. If there was a basic issue with your MCP2515 connection, you couldn't even switch into drive mode.

bakrimo, 2020-04-28:
Exactly

dexterbg, 2020-04-28:
A quick duck reveals this NiRen/Nano guide: https://circuitdigest.com/microcontroller-projects/arduino-can-tutorial-interfacing-mcp2515-can-bus-module-with-arduino

bakrimo, 2020-05-03:
You are right was hardware problem, "Nano cheap quality built".
Now it's showing battery level on dashboard full,  but I don't receive command from Pin9 relay sevcon supply to turn relay on
Any suggestions!

bakrimo, 2020-05-08:
What about "ecu ok" should connect to 12v bms by 10kohm resistant or 470 ohm

dexterbg, 2020-05-09:
Check out the example: https://github.com/dexterbg/Twizy-Virtual-BMS/blob/master/extras/Arduino-Example-Yazaki-Relays.pdf

bakrimo, 2020-05-10:
First thank for your reply
I did this example, when I turn the ignition On it shows battery level on dashboard everything OK and N flashing. When I turn key to start position nothing happens, and I tested relay K1 sevcon supply doesn't click (doesn't receive order to work)

bakrimo, 2020-05-14:
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
That is the charger I have on twizy, you think simplebms can work with it

dexterbg, 2020-05-16:
There are no known charger incompatibilities.

bakrimo, 2020-05-16:
Anyway when I plug 🔌 220v the charger wouldn't give 60v to traction battery only 13.5v to the 12v battery. Does it need signal from can_bus?
Or the charger damaged

dexterbg, 2020-05-16:
Yes of course it needs the CAN handshake with the BMS, that's what this project & repository is all about. See protocol documentation in the extras folder. I can only help you with the software if you provide debug details.

bakrimo, 2020-05-18:
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
Hopefully will help

bakrimo, 2020-05-20:
Do we  have to code the BMS battery to the rest of the vehicle…charger and Inverter doesn’t recognize the BMS

dexterbg, 2020-05-21:
Taking photos of the serial log is really weird. You can simply copy the serial log output.

But regarding the log, that looks perfectly normal & correct. So there doesn't seem to be a CAN or software issue, except if you would have configured the wrong output port for the 3MW relay. But you would already have noticed the 3MW relay doesn't work, wouldn't you?

If 3MW is OK, you should check if the CAN transmissions of the VirtualBMS really get to the bus. And you should check all charger and inverter wirings to the BMS, probably also check the relays.

bakrimo, 2020-05-22:
Every things looks good with the wires.
But when the key on M position N keep flashing is it normal?
And when I turn key to start position like anything at all happens

bakrimo, 2020-05-28:
Actually 3MW relay once I turned the ignition to position ON it turned off. And the and the STOP LIGHT WITH 3 BEEPS

Closed 2022-02-03.

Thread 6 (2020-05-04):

Twizy battery

Tudy1983, 2020-05-04:
Hi all im im new in this and I have some questions about twizy battery first in /if I take a battery from other twizy will work? Second is were I find the code? Becouse I buy all the staff to build my self one Thanks you all sorry for my bad English

dexterbg, 2020-05-09:
1. Yes, Twizy batteries can be exchanged between vehicles.
2. See https://github.com/dexterbg/Twizy-Virtual-BMS#installation

Closed 2022-02-03.

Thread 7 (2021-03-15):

Caricatore twizy

Tudy1983, 2021-03-15:
Hi a little question  is possible that the chargers won't work on difrent twizys ?I mean if I take a new charger will work on my twizy? Because I u buy a new one and it doesn't work

dexterbg, 2021-03-15:
This isn't a Twizy support forum, please post there.

Closed 2021-03-15.

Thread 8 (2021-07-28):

Hi Dexter after long time

Kamsta99, 2021-07-28:
After using Twizy for 1.5 year and doing 19 500 km, i did improved Arduino project still based on SimpleBMS, with very precise voltage meter (0.03 voltage accuracy), because used way is way to unprecise to use (0.3-1v accuracy) based on voltage delivered to Arduino and temperature. I expanded project with multiple security option like 3 temperature sensors, various temperature alerts and limitations, with use of ads1115 to have precise voltage based on project: https://www.youtube.com/watch?v=10QtHh6UNBs, merged toggeder. I want send you soon my project to use :)
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

I want to ask you, did its possible to control range showed in Twizy by battery ?! If yes tell me how pls :D

dexterbg, 2021-07-29:
Nice :-)

> I want to ask you, did its possible to control range showed in Twizy by battery ?!

Not to my knowledge. AFAIR the Twizy display unit calculates the range by itself from the distance driven and the SOC consumed.

Kamsta99, 2021-07-29:
That sad, i found that here but i dont know how interfere with that
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

Kamsta99, 2021-07-29:
[SimpleBMS.zip](https://github.com/dexterbg/Twizy-Virtual-BMS/files/6900315/SimpleBMS.zip)

Kamsta99, 2021-07-29:
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

Problem is i drived on single charge 91 km but on display show max 30 km range

mucahitdemir, 2022-01-05:
Hi! I think mathematical expressions for displaying _taken range_ may lead to wrong results.
In addition, can you debug this calculation by _stepping into_ function and _stepping over_ till the end?
You can track the problems on STM32 IDE or System Workbench IDE through debug options.
Best,
MD

Closed 2022-02-03.

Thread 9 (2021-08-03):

Twizy sevcon voltage limit

Kamsta99, 2021-08-03:
Source: https://github.com/dexterbg/Twizy-Virtual-BMS/blob/master/extras/SEVCON-Configuration.md
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
I tried doing this via Ovms, no success still cutsoff after 39 V

Patient:
Twizy, 2012 ,custom 8.7 kwh battery,

What i tried already:
Setting Twizy same as for applying tuning (no switching to GO)
In shell:
1. enable <pass>
2. xrt cfg pre
3. xrt cfg write 2c02 01 592
4. xrt cfg write 2c02 02 560
5. says --> OK, value edited is same as we set
6. xrt cfg op
7. But still cutsoff, with STOP light and SEVCON low voltage error

Tried also standalone
xrt cfg write 2c02 01 592
xrt cfg write 2c02 02 560
but no clue how to get this to work

dexterbg, 2021-08-04:
I'm afraid you're the first to actually try running the Twizy on such a low voltage. It's possible the Renault SEVCON firmware has some fixed internal limits to protect their battery, so the SDOs do not work as expected.

Another option is there is another SDO you need to change. Check out the "master dictionary" from the DVT software, maybe you can find some matching description.

Kamsta99, 2021-08-07:
Thanks for reply, where i can get DVT software for not 500$ and stuff
needed for that also?

śr., 4 sie 2021 o 08:39 Michael Balzer ***@***.***>
napisał(a):

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

Kamsta99, 2021-08-07:
Did we able to reprogram (unlock speed for example or torque) sevcon after
july 2016 with DVT software and usb dongle ?

sob., 7 sie 2021 o 13:00 Kamil Stankiewicz ***@***.***> napisał(a):

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

dexterbg, 2021-08-07:
a) Search the web, b) no.

Closed 2022-02-03.

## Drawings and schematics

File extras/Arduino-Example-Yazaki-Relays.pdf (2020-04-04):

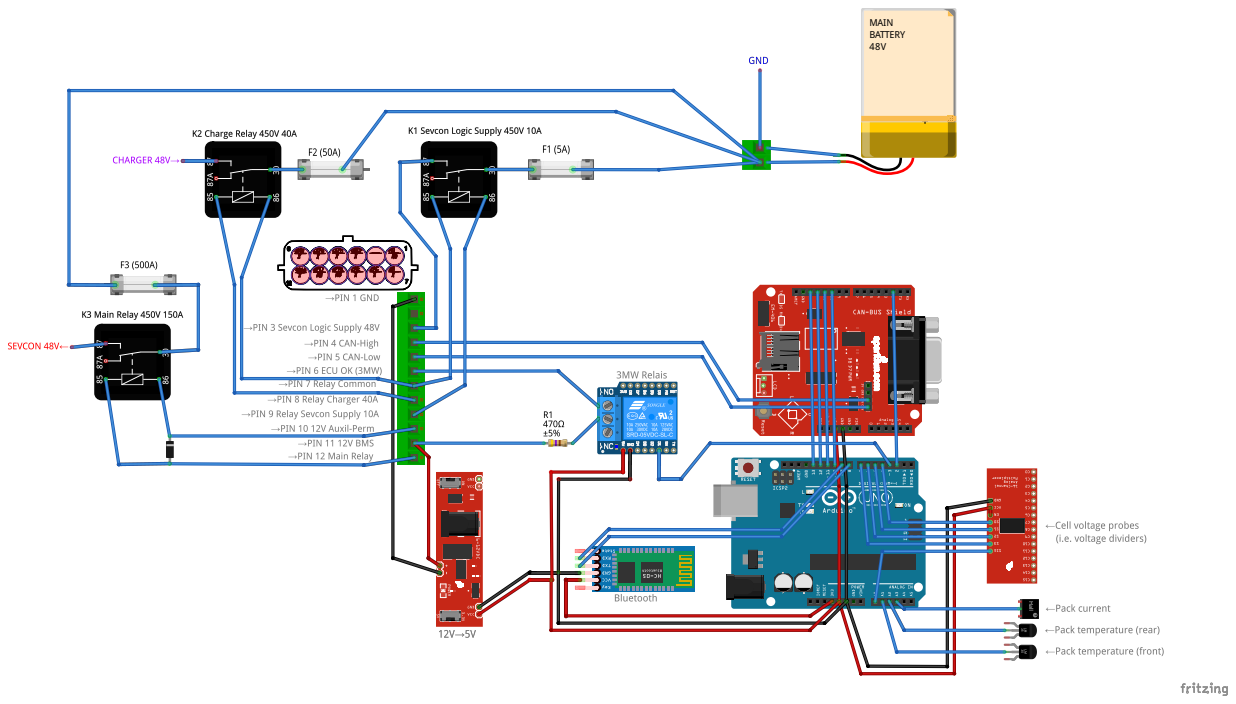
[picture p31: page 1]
MAIN BATTERY 48V

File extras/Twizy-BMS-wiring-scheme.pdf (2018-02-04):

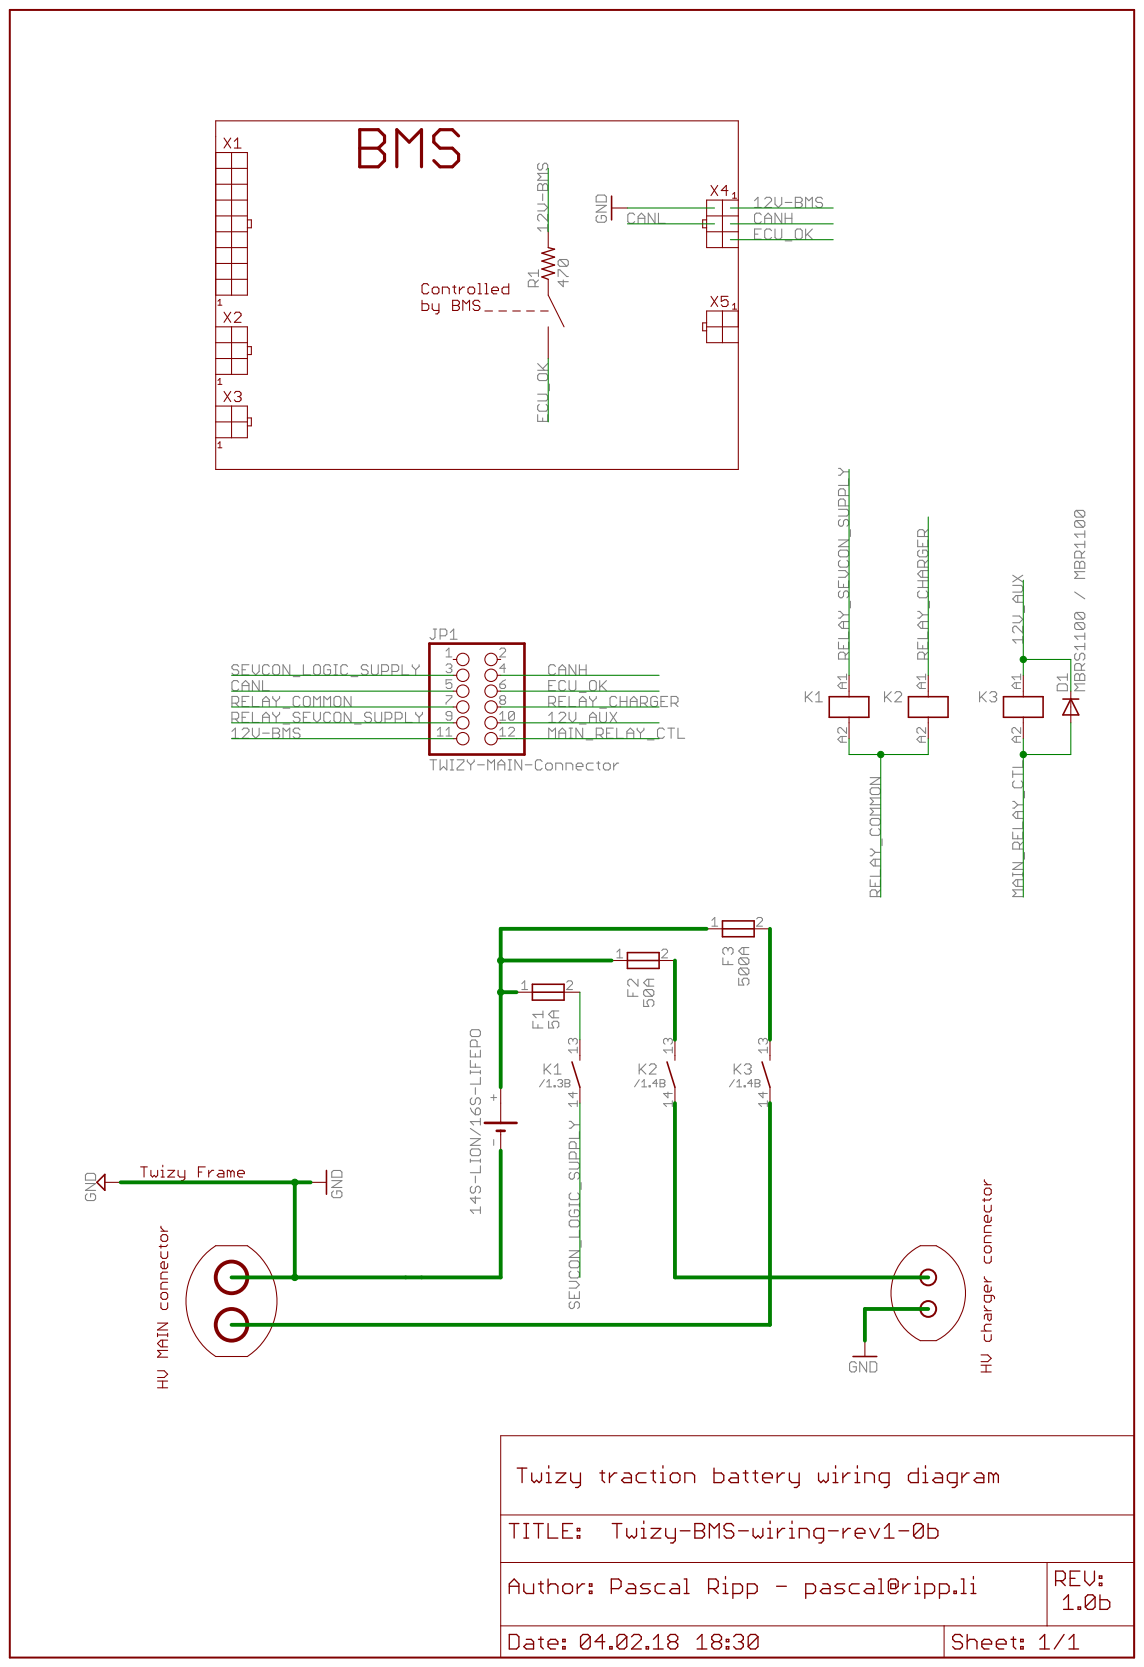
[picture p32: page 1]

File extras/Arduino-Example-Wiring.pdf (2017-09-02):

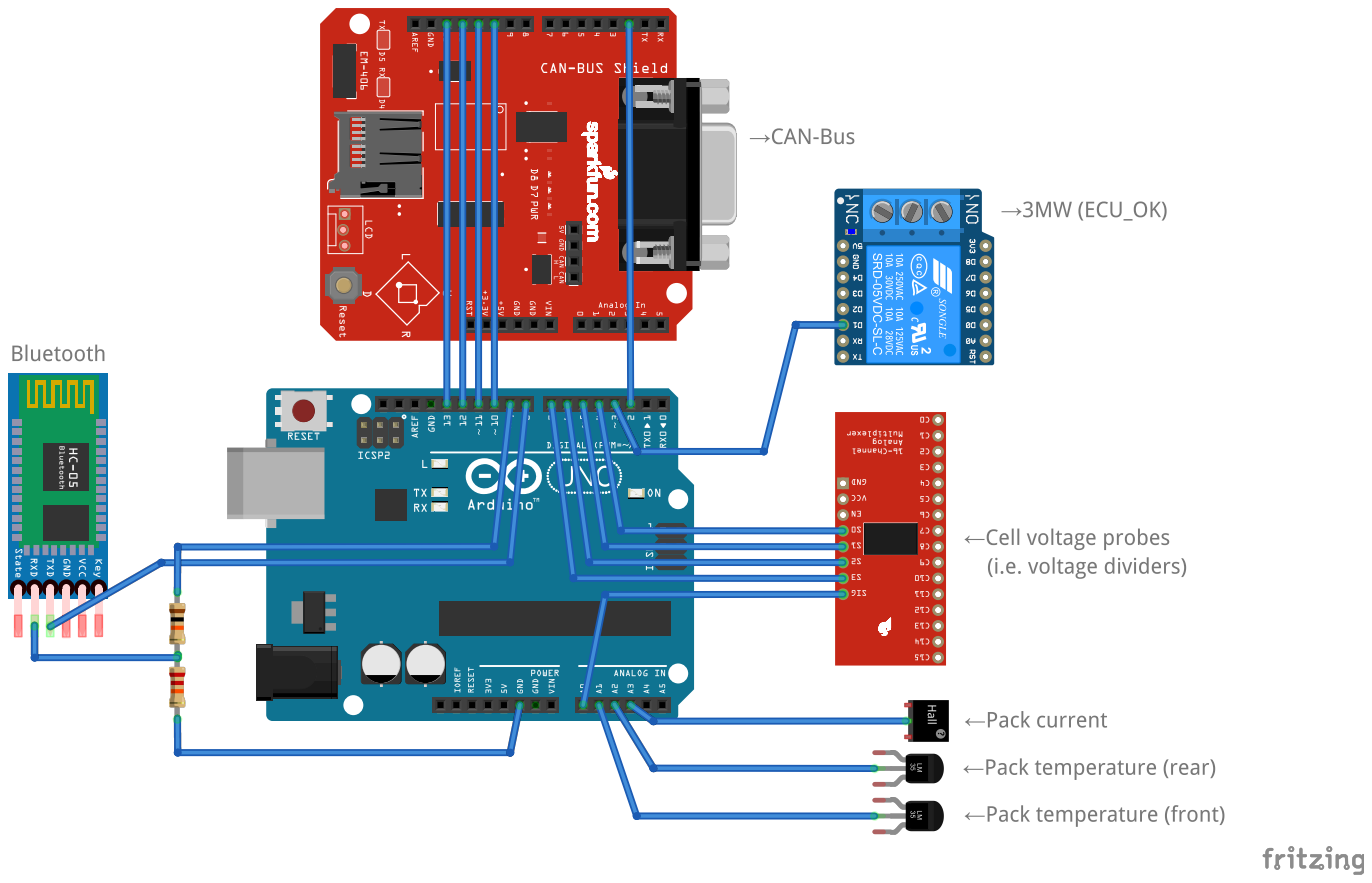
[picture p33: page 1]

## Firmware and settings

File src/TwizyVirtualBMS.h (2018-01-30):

/**
 * ==========================================================================
 * Twizy Virtual BMS
 * ==========================================================================
 * 
 * Emulation of Renault Twizy BMS (battery management system)
 * Interface between the Twizy and custom built / third party batteries
 * 
 * Author: Michael Balzer <dexter@dexters-web.de>
 * 
 * Twizy CAN object dictionary:
 * https://docs.google.com/spreadsheets/d/1gOrG9rnGR9YuMGakAbl4s97a6irHF6UNFV1TS5Ll7MY/edit#gid=0
 * (Maintainer: Michael Balzer <dexter@dexters-web.de>)
 * 
 * Twizy BMS CAN & hardware protocol decoding and reengineering has been done 
 * by a joint effort of (in reverse alphabetical order):
 *  - Lutz Schäfer <aquillo@t-online.de>
 *  - Pascal Ripp <pascal@ripp.li>
 *  - Bernd Eickhoff <b.eickhoff@gmx.de>
 *  - Michael Balzer <dexter@dexters-web.de>
 * 
 * Libraries used:
 *  - MCP_CAN: https://github.com/coryjfowler/MCP_CAN_lib
 * …plus one of…
 *  - TimerOne: https://github.com/PaulStoffregen/TimerOne
 *  - FlexiTimer2: https://github.com/PaulStoffregen/FlexiTimer2
 *  - TimerThree: https://github.com/PaulStoffregen/TimerThree
 * 
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
 */

#ifndef _TwizyVirtualBMS_h
#define _TwizyVirtualBMS_h

#define TWIZY_VBMS_VERSION      "V1.4.4 (2018-01-21)"

#ifndef TWIZY_TAG
#define TWIZY_TAG               "twizy."
#endif

#include <Arduino.h>
#include <avr/pgmspace.h>

#include <mcp_can.h>
#include <mcp_can_dfs.h>

#ifndef _TwizyVirtualBMS_config_h
#warning "Fallback to default TwizyVirtualBMS_config.h -- you should copy this into your sketch folder"
#include "TwizyVirtualBMS_config.h"
#endif

#ifndef TWIZY_USE_TIMER
#define TWIZY_USE_TIMER 1
#endif

#if TWIZY_USE_TIMER == 1
#include <TimerOne.h>
#elif TWIZY_USE_TIMER == 2
#include <FlexiTimer2.h>
#elif TWIZY_USE_TIMER == 3
#include <TimerThree.h>
#else
#error "TWIZY_USE_TIMER invalid, please set to 1, 2 or 3!"
#endif

// ==========================================================================
// TEST CONFIGURATION
// ==========================================================================

#ifndef TWIZY_3MW_PULSE_START
#define TWIZY_3MW_PULSE_START     58
#define TWIZY_3MW_PULSE_LOW       41
#define TWIZY_3MW_PULSE_155_A     31
#define TWIZY_3MW_PULSE_HIGH       6
#define TWIZY_3MW_PULSE_155_9      1
#endif

#ifndef TWIZY_SEND_INIT_FRAMES
#define TWIZY_SEND_INIT_FRAMES     1
#endif


// ==========================================================================
// TYPES AND CONSTANTS
// ==========================================================================


// Standard BMS types for setInfoBmsType():
// Note: contact us to allocate a reserved id for your BMS
enum TwizyBmsType {
  bmsType_VirtualBMS,
  bmsType_EdriverBMS,
  bmsType_reserved2,
  bmsType_reserved3,
  bmsType_reserved4,
  bmsType_reserved5,
  bmsType_reserved6,
  bmsType_undefined // 7 = do not send extended info frame
};


// Standard informational error codes for setInfoError():
// Note: add custom codes beginning at 128
enum TwizyBmsError {
  bmsError_None,
  bmsError_EEPROM,
  bmsError_SensorFailure,
  bmsError_VoltageHigh,
  bmsError_VoltageLow,
  bmsError_VoltageDiff,
  bmsError_TemperatureHigh,
  bmsError_TemperatureLow,
  bmsError_TemperatureDiff,
  bmsError_ChargerTemperatureHigh
};


// Twizy states:
enum TwizyState {
  Off,
  Init,
  Error,
  Ready,
  StartDrive,
  Driving,
  StopDrive,
  StartCharge,
  Charging,
  StopCharge,
  StartTrickle,
  Trickle,
  StopTrickle
};

// Twizy state names:
const char twizyStateName[13][13] PROGMEM = {
  "Off",
  "Init",
  "Error",
  "Ready",
  "StartDrive",
  "Driving",
  "StopDrive",
  "StartCharge",
  "Charging",
  "StopCharge",
  "StartTrickle",
  "Trickle",
  "StopTrickle"
};


// Known error codes for setError():
// Note: these can be used singularly or be ORed to set multiple indicators.
// i.e. do setError(TWIZY_SERV_TEMP|TWIZY_SERV_STOP) to indicate
// a severely high temperature
#define TWIZY_OK            0x00000000    // clear all indicators
#define TWIZY_SERV          0x00eeee00    // set SERV indicator
#define TWIZY_SERV_12V      0x00eeee20    // set SERV + 12V battery indicator
#define TWIZY_SERV_BATT     0x00eeee40    // set SERV + main battery indicator
#define TWIZY_SERV_TEMP     0x00eeee80    // set SERV + temperature indicator
#define TWIZY_SERV_STOP     0x00eeff00    // set SERV + STOP indicator + beep


// User callbacks hooks:
typedef void (*TwizyEnterStateCallback)(TwizyState currentState, TwizyState newState);
typedef bool (*TwizyCheckStateCallback)(TwizyState currentState, TwizyState newState);
typedef void (*TwizyTickerCallback)(unsigned int clockCnt);
typedef void (*TwizyProcessCanMsgCallback)(unsigned long rxId, byte rxLen, byte *rxBuf);


// ==========================================================================
// LIBRARY CODE AREA
// ==========================================================================

// PROGMEM string helpers:
#define FLASHSTRING     const __FlashStringHelper
#define FS(x)           (__FlashStringHelper*)(x)

#if TWIZY_DEBUG_LEVEL >= 1
  // Parameter boundary check with error output:
  #define CHECKLIMIT(var, minval, maxval) \
    if (var < minval || var > maxval) { \
      Serial.print(TWIZY_TAG); \
      Serial.print(__func__); \
      Serial.print(F(": ERROR " #var "=")); \
      Serial.print(var); \
      Serial.println(F(" out of bounds [" #minval "," #maxval "]")); \
      return false; \
    }
#else
  // Parameter boundary check with quiet error:
  #define CHECKLIMIT(var, minval, maxval) \
    if (var < minval || var > maxval) { \
      return false; \
    }
#endif


// -----------------------------------------------------
// Interrupt handlers
// 

volatile bool twizyCanMsgReceived = false;

#ifdef TWIZY_CAN_IRQ_PIN
void twizyCanISR() {
  twizyCanMsgReceived = true;
}
#endif

volatile bool twizyClockTick = false;

void twizyClockISR() {
  twizyClockTick = true;
}



// -----------------------------------------------------
// TwizyVirtualBMS class definition
// 

class TwizyVirtualBMS {
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

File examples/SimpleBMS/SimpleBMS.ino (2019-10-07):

/**
 * ==========================================================================
 * Twizy Virtual BMS Example: SimpleBMS
 * ==========================================================================
 *
 * - Derive SOC and power control from pack voltage measured using a
 *   simple voltage divider connected to an analog port.
 * - Measure pack temperature using a simple temperature sensor (LM35D)
 *   and issue temperature and STOP warnings accordingly.
 * 
 * Author: Michael Balzer <dexter@dexters-web.de>
 * 
 * Libraries used:
 *  - TwizyVirtualBMS: https://github.com/dexterbg/Twizy-Virtual-BMS
 *  - MCP_CAN: https://github.com/coryjfowler/MCP_CAN_lib
 *  - TimerOne: https://github.com/PaulStoffregen/TimerOne
 * 
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
 */

#include "TwizyVirtualBMS_config.h"
#include "TwizyVirtualBMS.h"

TwizyVirtualBMS twizy;


// -----------------------------------------------------
// Configuration
// 

// Maximum driving & recuperation power limits to use [W]:
#define MAX_DRIVE_POWER       18000
#define MAX_RECUP_POWER       8000

// Maximum charge current to use [A]:
#define MAX_CHARGE_CURRENT    35

// Voltage range 0…100% for driving:
#define VMIN_DRV              42.0
#define VMAX_DRV              52.0

// Voltage range 0…100% for charging:
#define VMIN_CHG              42.0
#define VMAX_CHG              57.6

// Voltage analog input:
// i.e. voltage divider scaling 60V → 4.5V
// (you may need to add some tolerance correction factor)
#define PORT_VOLT             A0
#define SCALE_VOLT            (60.0 / 4.5 * 5.0)

// SOC smoothing samples:
#define SMOOTH_SOC_DOWN       30  // slow adaption to lower voltage
#define SMOOTH_SOC_UP         5   // fast adaption to higher voltage

// Temperature analog input:
// i.e. LM35D: 2…100 °C → 0…1.0 V  (10 mV/°C)
#define PORT_TEMP             A1
#define BASE_TEMP             2.0
#define SCALE_TEMP            (100.0 / 1.0 * 5.0)

// Temperature smoothing samples:
#define SMOOTH_TEMP           10


// -----------------------------------------------------
// Status
// 

float temp = 20.0;
float soc = 90.0;     // Note: needs to be below 100 to be able to start charging


// --------------------------------------------------------------------------
// Callback: handle state transition for BMS
//  - called by twizyEnterState() after Twizy handling
// Note: avoid complex operations, this needs to be fast.
// 
void bmsEnterState(TwizyState currentState, TwizyState newState) {
  
  // The charger will not start charging at SOC=100%, so lower a too
  // high SOC on wakeup to enable topping-off charges:
  if (currentState == Init && newState == Ready) {
    if (soc > 99) {
      soc -= 1;
      twizy.setSOC(soc);
      twizy.setChargeCurrent(5);
      Serial.print(F("bmsEnterState: soc lowered to "));
      Serial.println(soc, 2);
    }
  }
  
}


// --------------------------------------------------------------------------
// Callback: timer ticker
//  - called every 10 ms by twizyTicker() after twizy handling
//  - clockCnt cyclic range: 0 .. 2999 = 30 seconds (reset to 0 on Off/Init)
// Note: avoid complex operations, this needs to be fast.
// 
void bmsTicker(unsigned int clockCnt) {
  
  if (!twizy.inState(Off) && (clockCnt % 100 == 0)) {
    // per second:
    Serial.println(F("\nbmsTicker:"));
    
    float vpack, newsoc, newtemp;
    
    // read pack voltage:
    vpack = analogRead(PORT_VOLT) / 1024.0 * SCALE_VOLT;
    
    Serial.print(F("- vpack=")); Serial.println(vpack, 2);
    twizy.setVoltage(vpack, true);
    
    // derive SOC change from voltage:
    if (twizy.inState(Charging)) {
      newsoc = (vpack - VMIN_CHG) / (VMAX_CHG - VMIN_CHG) * 100.0;
    }
    else {
      newsoc = (vpack - VMIN_DRV) / (VMAX_DRV - VMIN_DRV) * 100.0;
    }
    
    // smooth SOC:
    if (newsoc < soc) {
      // slow adaption to lower voltages:
      soc = (soc * (SMOOTH_SOC_DOWN-1) + newsoc) / SMOOTH_SOC_DOWN;
    }
    else {
      // fast adaption to higher voltages:
      soc = (soc * (SMOOTH_SOC_UP-1) + newsoc) / SMOOTH_SOC_UP;
    }
    
    // sanitize...
    soc = constrain(soc, 0.0, 100.0);
    
    Serial.print(F("- soc=")); Serial.println(soc, 2);
    twizy.setSOC(soc);
    
    // derive power limits & charge current from SOC:
    if (soc >= 90.0) {
      // high SOC: scale down recuperation & charge power
      int recpwr = (100-soc) / 10.0 * MAX_RECUP_POWER;
      Serial.print(F("- recpwr=")); Serial.println(recpwr);
      twizy.setPowerLimits(MAX_DRIVE_POWER, recpwr);
      // charge automatically stops below 5.0 A, so keep min 5.0 until 100%:
      float chgcurr = (round(soc*100) == 10000) ? 0.0 : 5.0 + (100-soc) / 10.0 * (MAX_CHARGE_CURRENT-5.0);
      Serial.print(F("- chgcurr=")); Serial.println(chgcurr);
      twizy.setChargeCurrent(chgcurr);
    }
    else if (soc <= 20.0) {
      // low SOC: scale down drive power
      int drvpwr = soc / 20.0 * MAX_DRIVE_POWER;
      Serial.print(F("- drvpwr=")); Serial.println(drvpwr);
      twizy.setPowerLimits(drvpwr, MAX_RECUP_POWER);
      twizy.setChargeCurrent(MAX_CHARGE_CURRENT);
    }
    else {
      // normal SOC: allow max power & current
      twizy.setPowerLimits(MAX_DRIVE_POWER, MAX_RECUP_POWER);
      twizy.setChargeCurrent(MAX_CHARGE_CURRENT);
    }
    
    // read battery temperature:
    newtemp = BASE_TEMP + analogRead(PORT_TEMP) / 1024.0 * SCALE_TEMP;
    
    // smooth:
    temp = (temp * (SMOOTH_TEMP-1) + newtemp) / SMOOTH_TEMP;
    
    Serial.print(F("- temp=")); Serial.println(temp);
    twizy.setTemperature(temp, temp, true);
    
    // set error status if battery too hot:
    if (temp > 50) {
      twizy.setError(TWIZY_SERV_TEMP|TWIZY_SERV_STOP);
    }
    else if (temp > 40) {
      twizy.setError(TWIZY_SERV_TEMP);
    }
    else {
      twizy.setError(TWIZY_OK);
    }
    
  }
  
}


// -----------------------------------------------------
// SETUP
// 

void setup() {
  
  Serial.begin(1000000);
  
  twizy.begin();
  twizy.attachTicker(bmsTicker);
  twizy.attachEnterState(bmsEnterState);
  
  twizy.setPowerLimits(MAX_DRIVE_POWER, MAX_RECUP_POWER);
  twizy.setChargeCurrent(MAX_CHARGE_CURRENT);
  twizy.setSOH(100);
  twizy.setSOC(soc);
  twizy.setTemperature(temp, temp, true);
  twizy.setVoltage(50.0, true);
  twizy.setCurrent(0.0);
  twizy.setError(TWIZY_OK);
}


// -----------------------------------------------------
// MAIN LOOP
// 

void loop() {
  twizy.looper();
}

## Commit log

2017-06-10 Twizy Virtual BMS V1.0 RC2 (2017-06-10) - Conversion to Arduino library - Added CAN RX callback bmsProcessCanMsg() - Added twizySetError() and error codes - Using ROM strings to save RAM - Configurab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
    Version: 0.2 (2017-06-06)
    - 3MW pulse cycle
    - Separate states for trickle charging
    - CAN TX retries
    - Added bmsTicker() callback
    Version: 0.1 (2017-06-04)
    - Initial release
    [CAN-Objektverzeichnis.ods, Protocol.ods]
2017-06-10 - Spelling correction in wiring scheme
2017-06-17 Twizy Virtual BMS V1.0.0 (2017-06-17) - Added charger configuration info - Protocol documentation update on error codes - Added `Error` state for emergency shutdowns - Ticker callback also called in 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
    [Protocol.ods]
2017-06-27 Version: 1.1.0 - Added support for Timer2 & Timer3 (see config header) - Added `setCurrentQA()` API call (native=fast 1/4 A resolution)
2017-07-02 - Added Youtube video links for prototype
2017-07-04 - Fixed polling check for CAN modules without IRQ - Raised serial speed for examples to 1000000 baud
    [SimpleBMS.ino, Template.ino, TwizyVirtualBMS.h]
2017-07-09 - Added Arduino example wiring scheme
    [Arduino-Example-Wiring.fzz]
2017-07-29 Version 1.2.0:
    - Ticker increments clockCnt on exit (first hook call with clockCnt=0)
    - Protocol startup phase closer to original:
    - id155[0] set to 0xFF on Init
    - Transition from Init to Ready after 100 ms
    - 3MW timing changed to 200 ms
    - id155[3] update coupled to 3MW switch
    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
    [Protocol.ods]
2017-07-29 - Added Tamura L06P400S05 hall sensor to example parts
2017-08-17 - New API calls stateName(), stateName(state) - No out of bounds error messages in TWIZY_DEBUG_LEVEL 0 - Donors update
    [BlazejBMS.ino, TwizyVirtualBMS.h, TwizyVirtualBMS_config.h]
2017-09-02 Version 1.3.0: - Added support to generate extended info frame 0x700 - New API calls: setInfoBmsType(), setInfoState1(), setInfoState2(), setInfoError(), setInfoBalancing() - Added support for module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
2017-09-02 - Arduino example scheme: HC-0x BT module RX voltage level 3.3V
    [Arduino-Example-Wiring.fzz]
2017-10-19 - Fixed image and part number for main fuse holder in parts list (Thx to Otto)
2018-01-30 Version 1.4.4: - Solved issue #1 (charger compatibility) - Closer reproduction of init phase frames - Detection of wakeup & shutdown by CAN activity
    [TwizyVirtualBMS.h]
2018-01-30 Protocol.ods V1.1: added 155_2 & 3MW handshake
    [Protocol.ods]
2018-02-04 - Twizy-BMS-wiring-scheme v1.0b: correction for R1 & D1
2018-07-04 - Added relay PCB design by Pascal
2019-10-07 - SimpleBMS template fix (thanks to @Kamsta99)
    [SimpleBMS.ino]
2020-04-04 - Added wiring example with Yazaki plug & relays
    [Arduino-Example-Yazaki-Relays.fzz]

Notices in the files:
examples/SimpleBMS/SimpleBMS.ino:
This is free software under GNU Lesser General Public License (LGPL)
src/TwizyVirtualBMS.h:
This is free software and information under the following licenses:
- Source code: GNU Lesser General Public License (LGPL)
